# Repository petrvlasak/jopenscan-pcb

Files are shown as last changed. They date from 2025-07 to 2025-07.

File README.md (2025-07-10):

# [JOpenScan](https://github.com/petrvlasak/jopenscan?tab=readme-ov-file#jopenscan) - Pi Shield and Ringlight PCBs

These PCBs are compatible with the original [OpenScan](https://openscan.eu/) DIY 3D Scanner [firmware](https://openscan-org.github.io/OpenScan-Doc/firmware/setup/). They contain some improvements:

- Pi Shield
  - Proper current limiting resistors for MOSFETs in Ringlight control
  - Software shutdown of stepper motors (available only in [JOpenScan firmware](https://github.com/petrvlasak/jopenscan))
- Ringlight
  - Removed unnecessary current limiting resistors

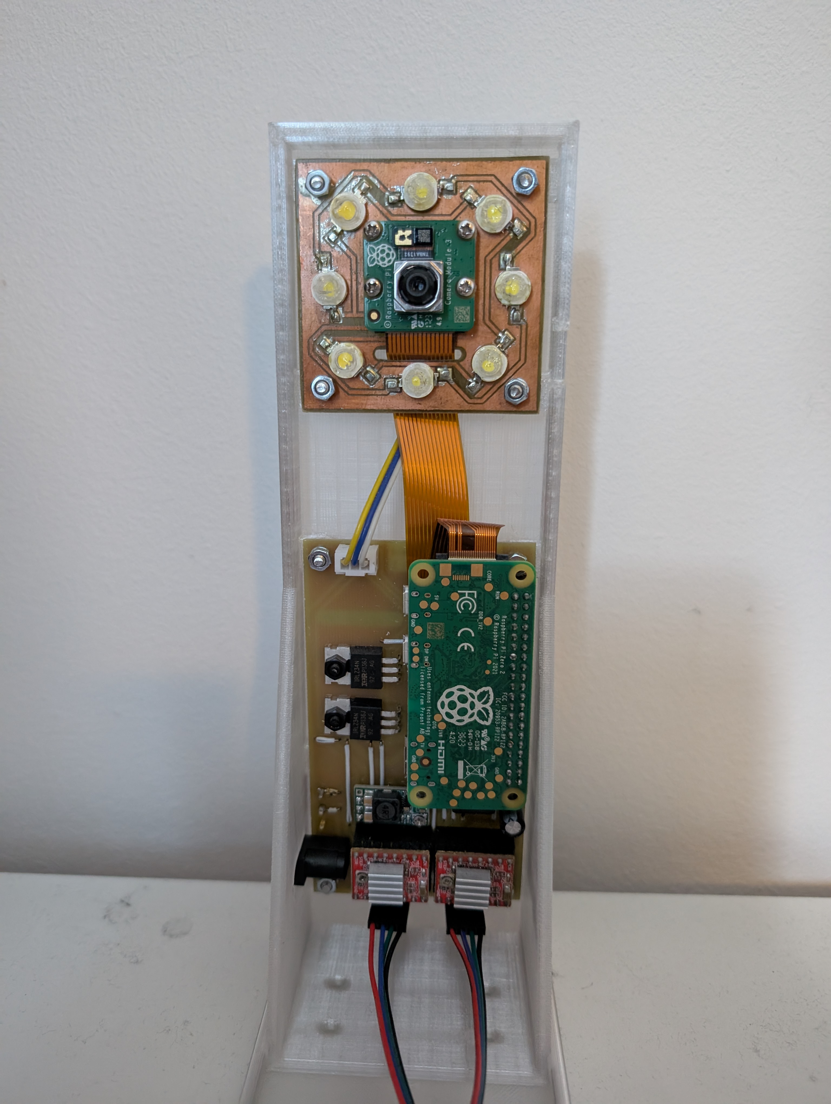
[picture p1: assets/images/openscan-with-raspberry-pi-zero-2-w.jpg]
OpenScan with Raspberry Pi Zero 2 W


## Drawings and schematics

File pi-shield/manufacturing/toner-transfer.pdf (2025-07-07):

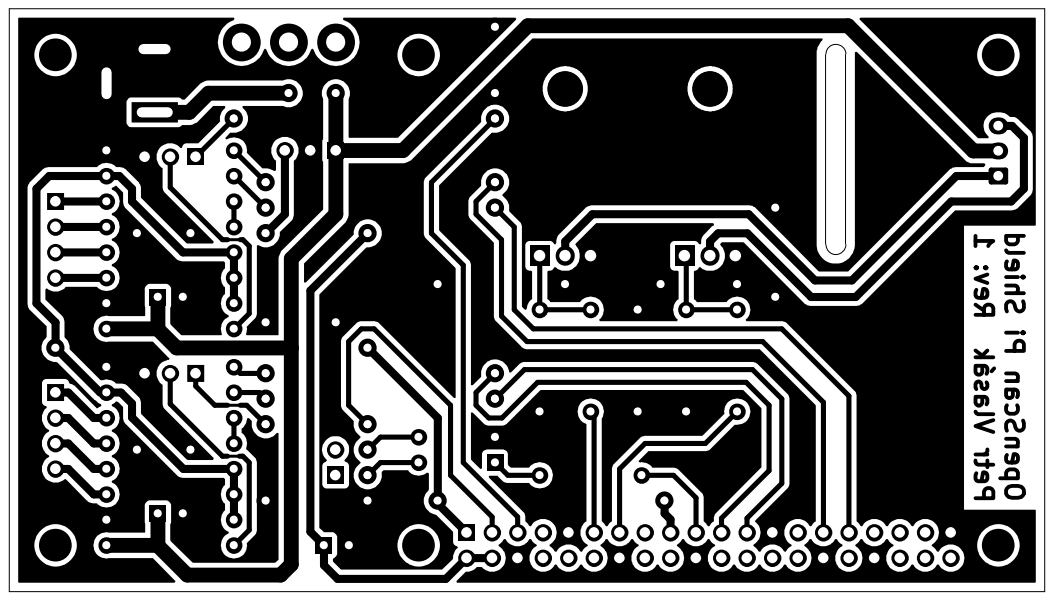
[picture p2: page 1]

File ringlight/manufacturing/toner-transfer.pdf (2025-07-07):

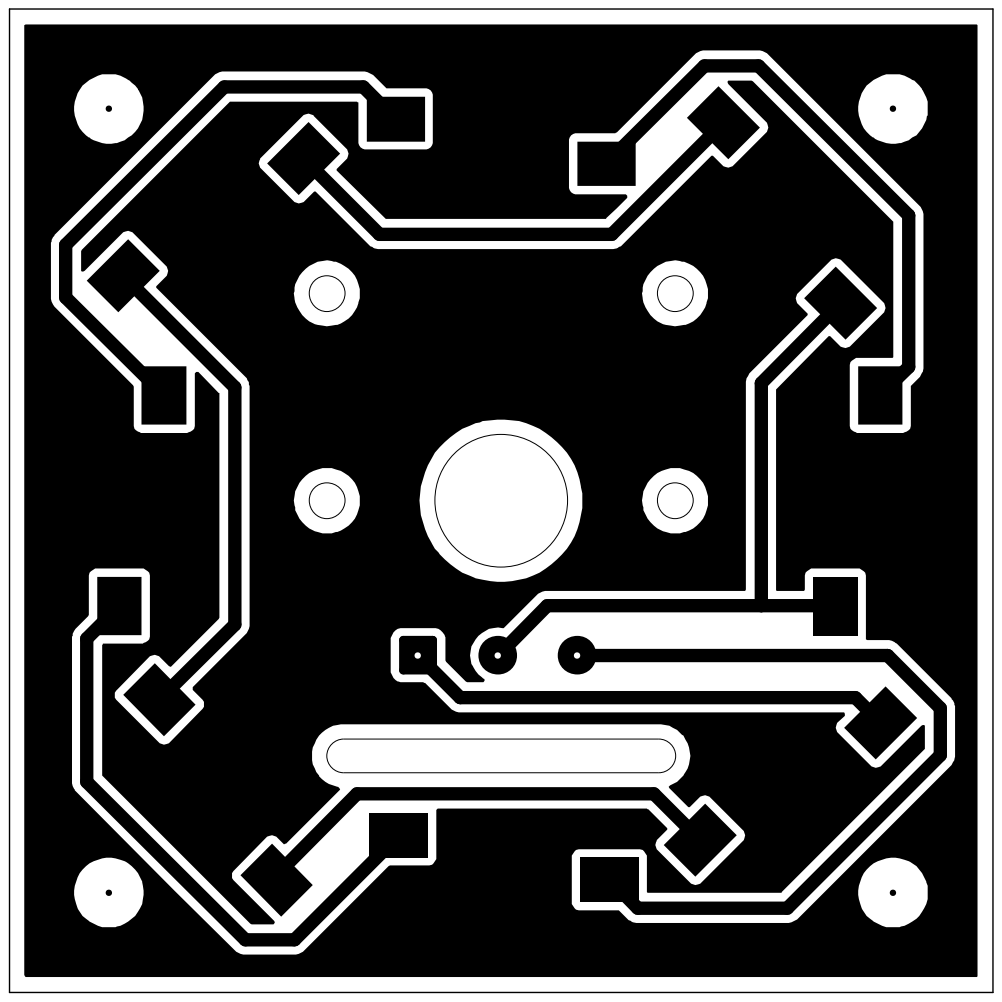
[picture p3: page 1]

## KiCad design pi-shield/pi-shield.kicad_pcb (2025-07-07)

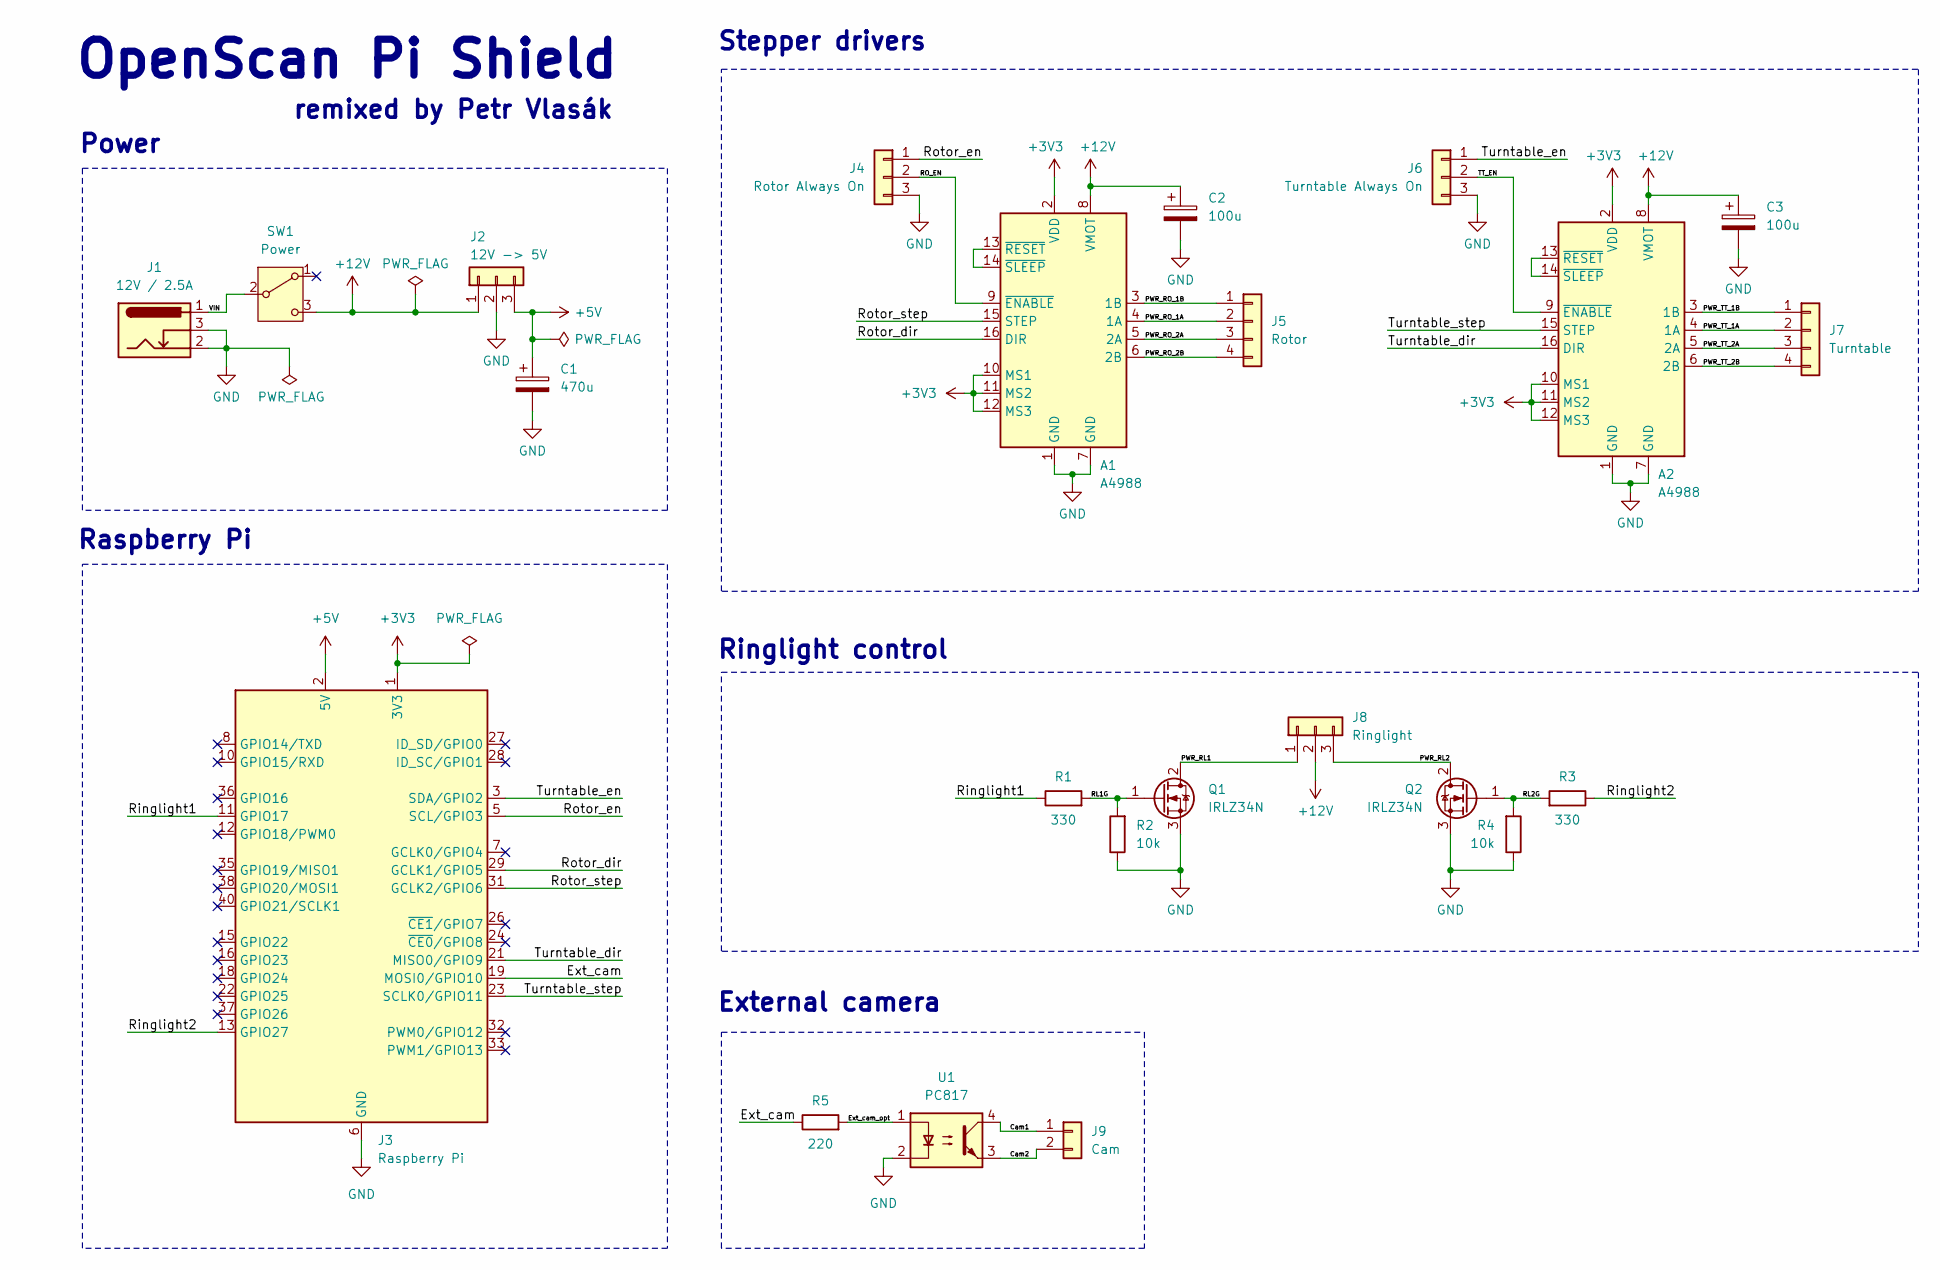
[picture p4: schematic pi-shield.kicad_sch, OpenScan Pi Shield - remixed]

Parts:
A1, A2: A4988
C1: 470u; CP_Radial_D6.3mm_P2.50mm
C2, C3: 100u; CP_Radial_D6.3mm_P2.50mm
J1: 12V / 2.5A; BarrelJack_GCT_DCJ200-10-A_Horizontal
J2: 12V -> 5V; PinHeader_1x03_P2.54mm_Vertical
J3: Raspberry Pi; PinSocket_2x20_P2.54mm_Vertical
J4: Rotor Always On; PinHeader_1x03_P2.54mm_Vertical
J5: Rotor; PinHeader_1x04_P2.54mm_Vertical
J6: Turntable Always On; PinHeader_1x03_P2.54mm_Vertical
J7: Turntable; PinHeader_1x04_P2.54mm_Vertical
J8: Ringlight; JST_XH_B3B-XH-A_1x03_P2.50mm_Vertical
J9: Cam; PinSocket_1x02_P2.54mm_Vertical
Q1, Q2: IRLZ34N; TO-220-3_Horizontal_TabDown
R1, R3: 330; R_Axial_DIN0207_L6.3mm_D2.5mm_P10.16mm_Horizontal
R2, R4: 10k; R_Axial_DIN0207_L6.3mm_D2.5mm_P10.16mm_Horizontal
R5: 220; R_Axial_DIN0207_L6.3mm_D2.5mm_P10.16mm_Horizontal
SW1: Power; SW_SPDT_CANAL_ELECTRONIC_SL19-121
U1: PC817; DIP-4_W7.62mm

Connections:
+3V3: A1.2 (VDD), A1.10 (MS1), A1.11 (MS2), A1.12 (MS3), A2.2 (VDD), A2.10 (MS1), A2.11 (MS2), A2.12 (MS3), J3.1 (3V3), J3.17 (3V3)
+5V: C1.1, J2.3, J3.2 (5V), J3.4 (5V)
+12V: A1.8 (VMOT), A2.8 (VMOT), C2.1, C3.1, J2.1, J8.2, SW1.3 (C)
/Cam1: J9.1, U1.4
/Cam2: J9.2, U1.3
/Ext_cam: J3.19 (MOSI0/GPIO10), R5.1
/Ext_cam_opt: R5.2, U1.1
/PWR_RL1: J8.1, Q1.2 (D)
/PWR_RL2: J8.3, Q2.2 (D)
/PWR_RO_1A: A1.4 (1A), J5.2
/PWR_RO_1B: A1.3 (1B), J5.1
/PWR_RO_2A: A1.5 (2A), J5.3
/PWR_RO_2B: A1.6 (2B), J5.4
/PWR_TT_1A: A2.4 (1A), J7.2
/PWR_TT_1B: A2.3 (1B), J7.1
/PWR_TT_2A: A2.5 (2A), J7.3
/PWR_TT_2B: A2.6 (2B), J7.4
/RL1G: Q1.1 (G), R1.2, R2.2
/RL2G: Q2.1 (G), R3.2, R4.2
/RO_EN: A1.9 (~ENABLE), J4.2
/Ringlight1: J3.11 (GPIO17), R1.1
/Ringlight2: J3.13 (GPIO27), R3.1
/Rotor_dir: A1.16 (DIR), J3.29 (GCLK1/GPIO5)
/Rotor_en: J3.5 (SCL/GPIO3), J4.1
/Rotor_step: A1.15 (STEP), J3.31 (GCLK2/GPIO6)
/TT_EN: A2.9 (~ENABLE), J6.2
/Turntable_dir: A2.16 (DIR), J3.21 (MISO0/GPIO9)
/Turntable_en: J3.3 (SDA/GPIO2), J6.1
/Turntable_step: A2.15 (STEP), J3.23 (SCLK0/GPIO11)
/VIN: J1.1, SW1.2 (B)
GND: A1.1 (GND), A1.7 (GND), A2.1 (GND), A2.7 (GND), C1.2, C2.2, C3.2, J1.2, J1.3, J2.2, J3.6 (GND), J3.9 (GND), J3.14 (GND), J3.20 (GND), J3.25 (GND), J3.30 (GND), J3.34 (GND), J3.39 (GND), J4.3, J6.3, Q1.3 (S), Q2.3 (S), R2.1, R4.1, U1.2
unnamed: A1.13 (~RESET), A1.14 (~SLEEP)
unnamed: A2.13 (~RESET), A2.14 (~SLEEP)

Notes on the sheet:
External camera
Power
remixed by Petr Vlasák
Ringlight control
OpenScan Pi Shield
Raspberry Pi
Stepper drivers

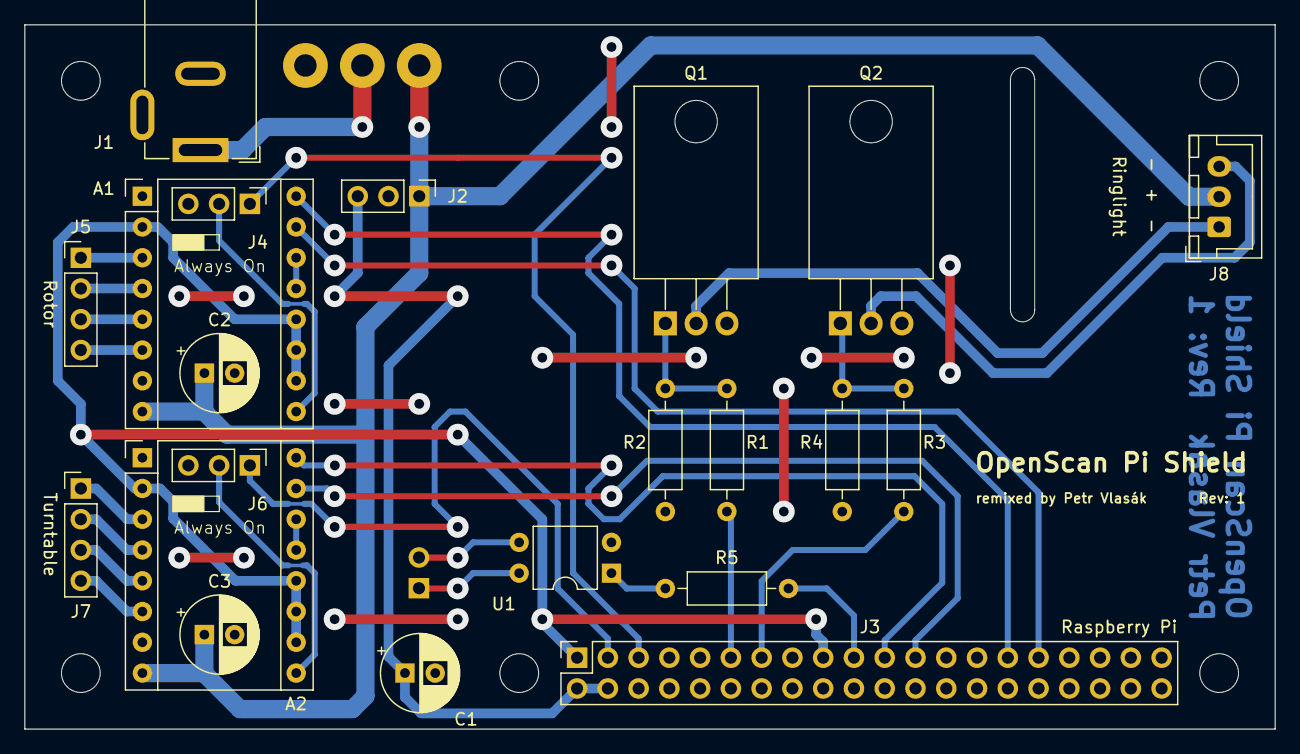
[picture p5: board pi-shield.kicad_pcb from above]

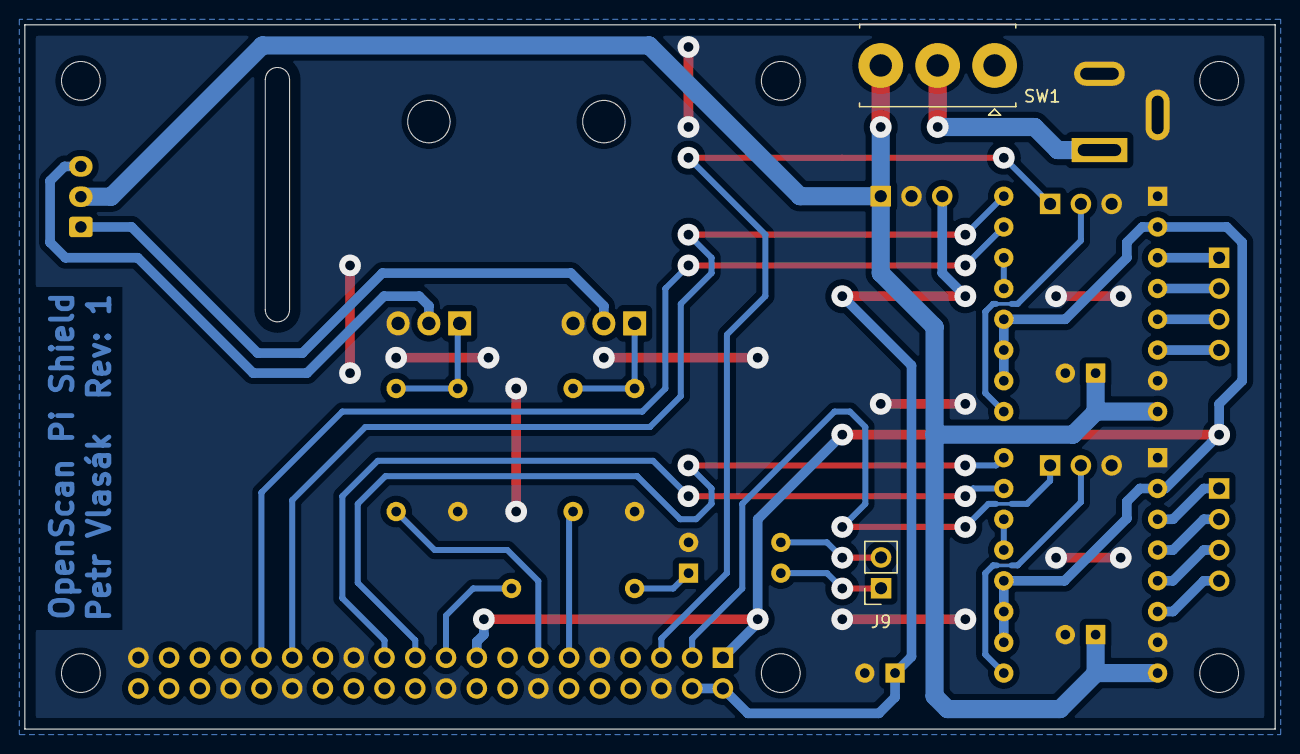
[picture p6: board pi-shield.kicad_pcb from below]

Board: 2 copper layers, 103.2 x 58.1 mm, 23 parts (2 on the bottom side), 33 nets.

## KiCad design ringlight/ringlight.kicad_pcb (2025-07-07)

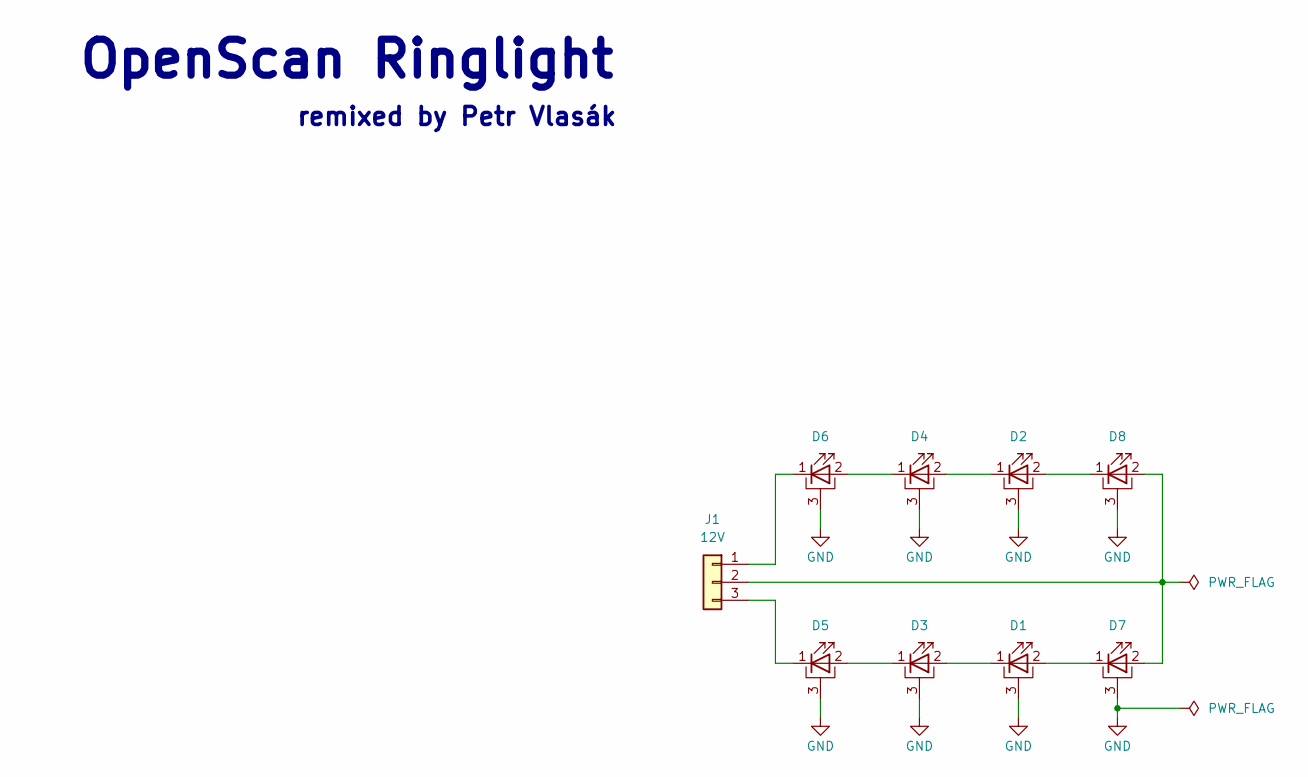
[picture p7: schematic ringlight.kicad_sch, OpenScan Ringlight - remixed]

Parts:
D1, D2, D3, D4, D5, D6, D7, D8: LED_Pad; LED_1W_3W_R8
J1: 12V; SolderWire-0.5sqmm_1x03_P4.8mm_D0.9mm_OD2.3mm

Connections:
GND: D1.3 (PAD), D2.3 (PAD), D3.3 (PAD), D4.3 (PAD), D5.3 (PAD), D6.3 (PAD), D7.3 (PAD), D8.3 (PAD)
unnamed: D1.2 (A), D7.1 (K)
unnamed: D1.1 (K), D3.2 (A)
unnamed: D2.2 (A), D8.1 (K)
unnamed: D2.1 (K), D4.2 (A)
unnamed: D3.1 (K), D5.2 (A)
unnamed: D4.1 (K), D6.2 (A)
unnamed: D5.1 (K), J1.3
unnamed: D6.1 (K), J1.1
unnamed: D7.2 (A), D8.2 (A), J1.2

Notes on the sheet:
remixed by Petr Vlasák
OpenScan Ringlight

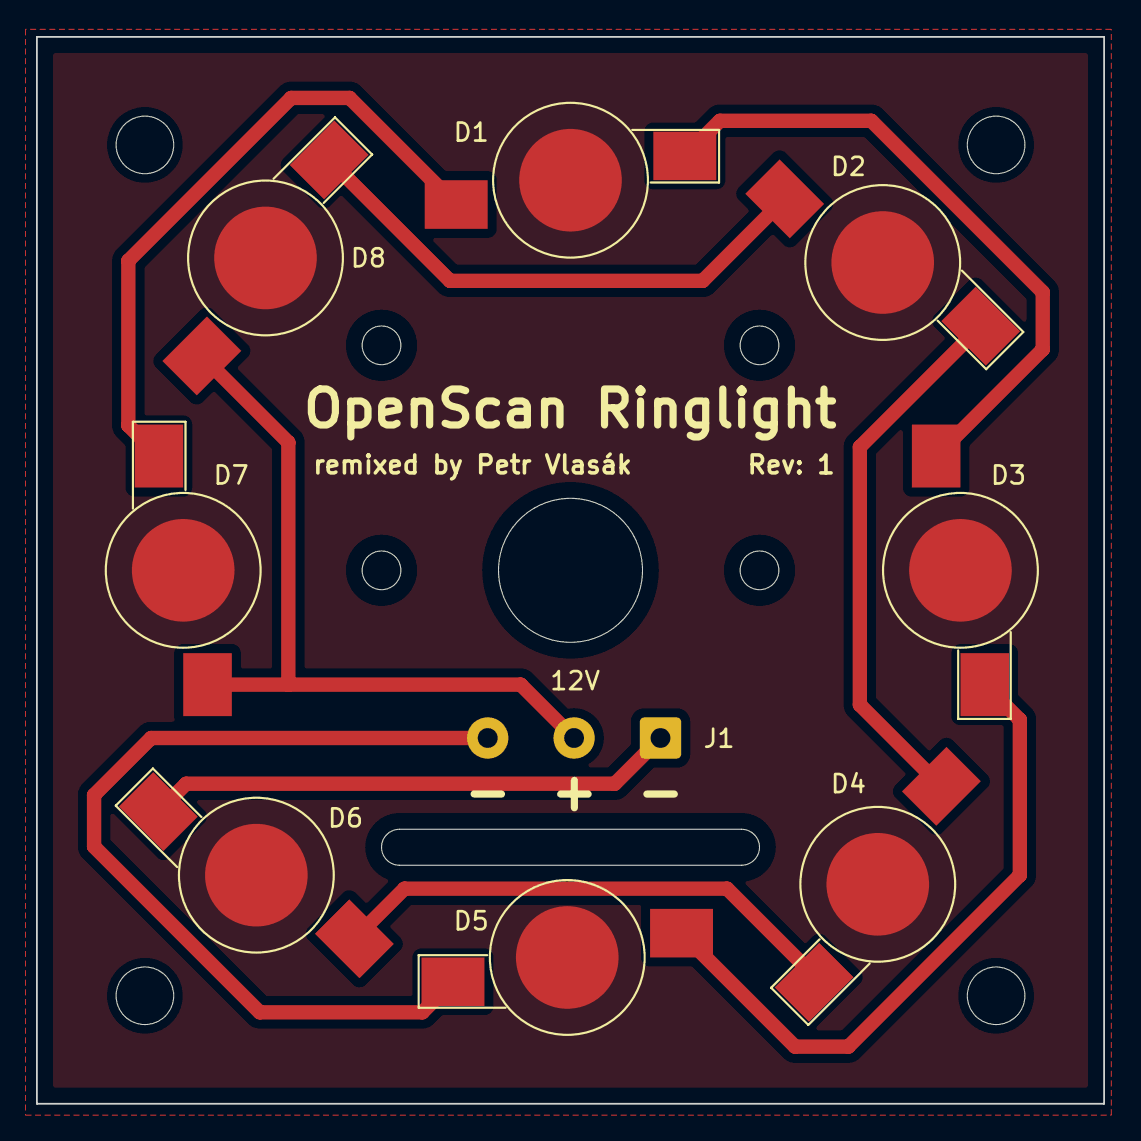
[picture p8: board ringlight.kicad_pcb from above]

Board: 2 copper layers, 59.3 x 59.3 mm, 9 parts (0 on the bottom side), 10 nets.

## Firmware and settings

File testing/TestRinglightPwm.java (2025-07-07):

///usr/bin/env jbang "$0" "$@" ; exit $?

//DEPS org.slf4j:slf4j-api:2.0.12
//DEPS org.slf4j:slf4j-simple:2.0.12
//DEPS com.pi4j:pi4j-core:2.6.0
//DEPS com.pi4j:pi4j-plugin-raspberrypi:2.6.0
//DEPS com.pi4j:pi4j-plugin-gpiod:2.6.0

import com.pi4j.Pi4J;
import com.pi4j.context.Context;
import com.pi4j.io.gpio.digital.DigitalOutput;
import com.pi4j.io.gpio.digital.DigitalState;
import com.pi4j.util.Console;

public class TestRinglightPwm {

    private static final int PIN_RL1 = 17;
    private static final int PIN_RL2 = 27;

    public static void main(String[] args) throws Exception {
        var console = new Console();
        var pi4j = Pi4J.newAutoContext();
        var ringlight1 = new Ringlight(pi4j, 1, PIN_RL1);
        var ringlight2 = new Ringlight(pi4j, 2, PIN_RL2);

        Runtime.getRuntime().addShutdownHook(new Thread(() -> {
            console.println("Terminating");
            ringlight1.thread.interrupt();
            ringlight2.thread.interrupt();
            try {
                ringlight1.thread.join();
            } catch (InterruptedException ignored) {}
            try {
                ringlight2.thread.join();
            } catch (InterruptedException ignored) {}
            console.println("Terminated");
        }, "app-shutdown"));

        int intensity = 1;
        boolean increasing = false;

        while (true) {
            if (intensity == 0) {
                increasing = true;
            }
            if (intensity == 100) {
                increasing = false;
            }
            if (increasing) {
                intensity++;
            } else {
                intensity--;
            }
            console.println("Ringlight 1: " + intensity);
            console.println("Ringlight 2: " + (100 - intensity));
            ringlight1.intensity = intensity;
            ringlight2.intensity = 100 - intensity;
            Thread.sleep(500);
        }
    }

    private static class Ringlight implements Runnable {

        private static final int PERIOD_NS = 1_000_000_000 / 100; // 100Hz
        private static final int VALUE_MULTIPLIER = PERIOD_NS / 100; // mapping value range 0-100 to period length
        private static final int SLEEP_NS = PERIOD_NS / 1000;

        private final DigitalOutput pin;
        private volatile int intensity;
        private Thread thread;

        private Ringlight(Context context, int ringlightNumber, int pinNumber) {
            pin = context.create(DigitalOutput.newConfigBuilder(context)
                    .id("rl" + ringlightNumber)
                    .name("Ringlight " + ringlightNumber)
                    .address(pinNumber)
                    .shutdown(DigitalState.LOW)
                    .initial(DigitalState.LOW));
            intensity = 0;
            thread = Thread.ofVirtual().start(this);
        }

        @Override
        public void run() {
            try {
                while (true) {
                    if (intensity == 100 && pin.isLow()) {
                        pin.high();
                    } else {
                        if (System.nanoTime() % PERIOD_NS < intensity * VALUE_MULTIPLIER) {
                            if (pin.isLow()) {
                                pin.high();
                            }
                        } else if (pin.isHigh()) {
                            pin.low();
                        }
                    }
                    if (Thread.interrupted()) {
                        throw new InterruptedException();
                    }
                    Thread.sleep(0, SLEEP_NS);
                }
            } catch (InterruptedException ignored) {}
        }

    }

}

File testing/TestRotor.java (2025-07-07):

///usr/bin/env jbang "$0" "$@" ; exit $?

//DEPS org.slf4j:slf4j-api:2.0.12
//DEPS org.slf4j:slf4j-simple:2.0.12
//DEPS com.pi4j:pi4j-core:2.6.0
//DEPS com.pi4j:pi4j-plugin-raspberrypi:2.6.0
//DEPS com.pi4j:pi4j-plugin-gpiod:2.6.0

import com.pi4j.Pi4J;
import com.pi4j.io.gpio.digital.DigitalOutput;
import com.pi4j.io.gpio.digital.DigitalState;

public class TestRotor {

    private static final int PIN_EN = 3;
    private static final int PIN_DIR = 5;
    private static final int PIN_STEP = 6;

    private static final int STEPS_PER_REV = 200 * 16;

    public static void main(String[] args) throws Exception {
        var pi4j = Pi4J.newAutoContext();
        var en = pi4j.create(DigitalOutput.newConfigBuilder(pi4j)
                .id("en")
                .name("Stepper Motor Enabled")
                .address(PIN_EN)
                .shutdown(DigitalState.HIGH)
                .initial(DigitalState.HIGH));
        var dir = pi4j.create(DigitalOutput.newConfigBuilder(pi4j)
                .id("dir")
                .name("Stepper Motor Direction")
                .address(PIN_DIR)
                .shutdown(DigitalState.LOW)
                .initial(DigitalState.LOW));
        var step = pi4j.create(DigitalOutput.newConfigBuilder(pi4j)
                .id("step")
                .name("Stepper Motor Step")
                .address(PIN_STEP)
                .shutdown(DigitalState.LOW)
                .initial(DigitalState.LOW));

        // Enable motor
        en.low();

        // Set motor direction clockwise
        dir.high();

        // Spin motor one rotation slowly
        for (int x = 0; x < (STEPS_PER_REV / 2); x++) {
            step.high();
            Thread.sleep(0, 500000);
            step.low();
            Thread.sleep(0, 500000);
        }

        // Pause for one second
        Thread.sleep(1000);

        // Set motor direction counterclockwise
        dir.low();

        // Spin motor two rotations quickly
        for(int x = 0; x < (STEPS_PER_REV / 2); x++) {
            step.high();
            Thread.sleep(0, 500000);
            step.low();
            Thread.sleep(0, 500000);
        }

        // Pause for one second
        Thread.sleep(1000);

        // Disable motor
        en.high();

        pi4j.shutdown();
    }

}

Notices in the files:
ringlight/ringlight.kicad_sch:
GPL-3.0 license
